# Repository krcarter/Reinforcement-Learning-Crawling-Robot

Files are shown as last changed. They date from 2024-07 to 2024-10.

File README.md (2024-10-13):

# Reinforcement Learning Crawling-Robot

Built a simple quadruped robot that used reinforcement learning for walking. I trained the robot in [Pybullet](https://docs.google.com/document/d/10sXEhzFRSnvFcl3XxNGhnD4N2SedqwdAvK3dsihxVUA/edit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).

Youtube Video: [https://youtu.be/Dv9h6W830aU?si=A5QDVAJMPijuq6lc](https://youtu.be/Dv9h6W830aU?si=A5QDVAJMPijuq6lc)

Table_Crawl  

Pronk Gait 

# Hardware

 URDF files are in the models folder. CAD files (step & STL) are in the hardware folder

# Python Dependencies

* pybullet==3.2.6 (For windows need to also install Microsoft C++ Build Tools)
* matplotlib==3.6.3
* numpy==1.26.4
* gym==0.23.1
* tensorflow == 2.17.0
* stable-baselines3 == 2.3.2
* shimmy == 0.2.1

# Setting up the Training Enviornment

Pronk Sim 

Pybullet's documentation was a little hard for me to first understand on how to setup the learning enviornment. Two main things is 

* initializing the enviornment in the `_init_.py` in the pybullet_envs folder

```
C:\Users\My PC\AppData\Local\Programs\Python\Python311\Lib\site-packages\pybullet_envs
```

Code to add to the `_init_.py`

```
register(
    id='CrawlingRobot-v0',
    entry_point='pybullet_envs:RobotEnv',
    max_episode_steps=1000,
    reward_threshold=1000.0
)
```

* Creating the `robot_env.py`. This is the big code on how to initilize robot into world how to reset, how to step simulation, how to get robot observation, and how to computer reward. This is is the main script that has to be modified

This script also has to be placed inside the pybullet_envs folder

# References (Cool papers)

* Kamidi, Vinay R., Wael Saab, and Pinhas Ben-Tzvi. "Design and analysis of a novel planar robotic leg for high-speed locomotion." 2017 IEEE/RSJ International Conference on Intelligent Robots and Systems (IROS). IEEE, 2017.

* Singla, Abhik, et al. "Realizing learned quadruped locomotion behaviors through kinematic motion primitives." 2019 International Conference on Robotics and Automation (ICRA). IEEE, 2019.

* Tan, Jie, et al. "Sim-to-real: Learning agile locomotion for quadruped robots." arXiv preprint arXiv:1804.10332 (2018).

* Rudin, Nikita, et al. "Learning to walk in minutes using massively parallel deep reinforcement learning." Conference on Robot Learning. PMLR, 2022.

* Schulman, John, et al. "Proximal policy optimization algorithms." arXiv preprint arXiv:1707.06347 (2017).

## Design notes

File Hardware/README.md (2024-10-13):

# Hardware

 To create your own custom URDF for bullet using fusion 360 for CAD checkout this github repo

 * https://github.com/yanshil/Fusion2PyBullet (Need to change the color, remove transmissions)

## Bill of Materials
 
 Amazon affiliate links
 
 [Crawling Robot Bill of Materials](https://docs.google.com/spreadsheets/d/1Qh913g_B4fr31vWqntHaWgeFabi9nsJZdBvG8iXUXsA/edit?usp=sharing)

 1. [4x MG-995 Servos Motors](https://amzn.to/4dJvymz)
 2. [Arduino Uno](https://amzn.to/487Hr4Q)
 3. [PCA9685 Servo Board](https://amzn.to/3Nohsw9)
 4. [2s Lipo Battery 50C 2200mAh](https://amzn.to/3YlSpQM)

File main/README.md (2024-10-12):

# Introduction

This is where the code lies for both the manual and reinforcement learning scripts. First, this code is very rough and was first pass, riddled with a pleothra of bad coind practices. However, this is not production code and is meant to showcase ideas.

## Manual Walking

The two scripts for the manual walking is done in files `ellipsoid_traj_small.py` and `ellipsoid_traj_long.py`

In these scripts is where the math to generate the ellipsoid and then using the forward and inverse kinematics of the legs turn the ellisoid x and y trajectory to joint coordinates for the legs.

The output of the script is done in function 

```
def sim_to_real_text_file(trajectory, num_steps):

```

This outputs a csv and a text file in the format needed to upload to arduino for the joint trajectories that will need to be followed in the Arduino code.

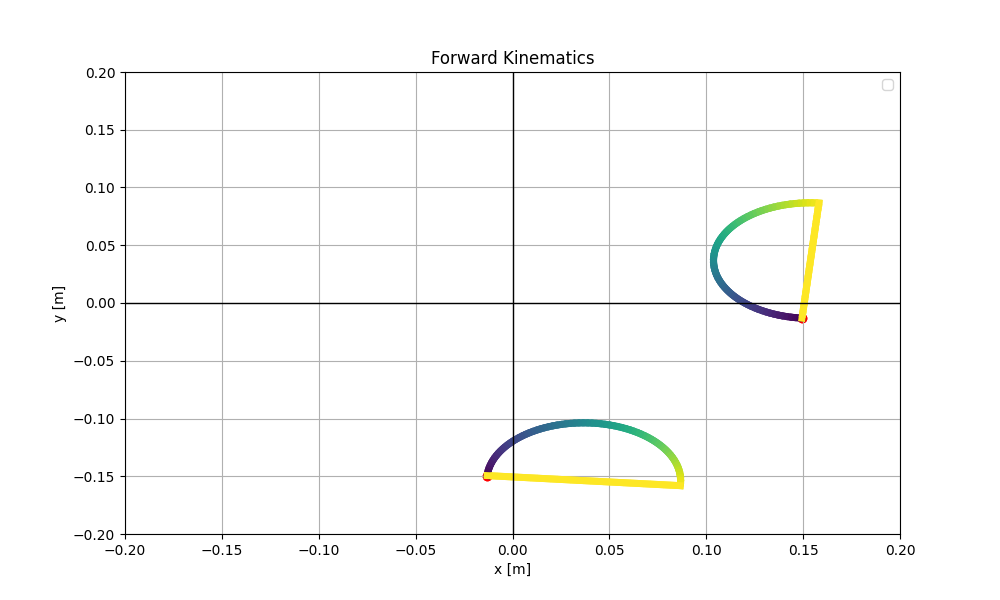
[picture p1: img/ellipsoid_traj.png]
Ellipsoid
 

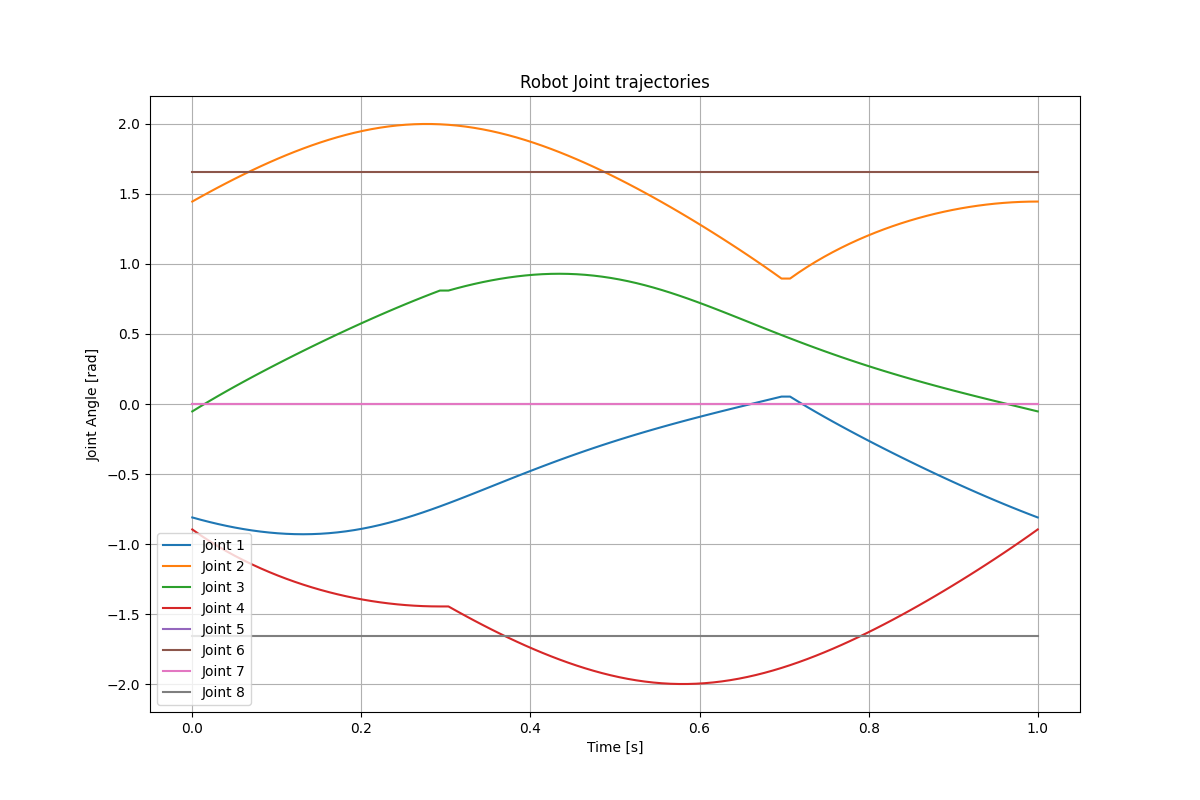
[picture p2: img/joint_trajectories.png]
Joint Trajectories
 

## Running the training

The reinforcement learning pipeline to generate trajectories to put on the robot was running `robot_train.py`, `robot_evaluate.py`, and then `robot_csv_simulation.py`. Also, the `robot_env.py`

### robot_env.py

The create of the enviornment is one of the biggest steps of the pipeline. Some things are probably easiest to adjust are the, action space limits as this controls the minimum and max value of the leg positions

```
action_low  = np.array([ -75,  30,  0, -120, 0,  70, 0, -110]) * np.pi/180
action_high = np.array([   0, 120, 75,  -30, 0,  110, 0,-70]) * np.pi/180
```

Also adjusting the rewards

```
reward = (self._distance_weight * forward_reward 
                  - self._energy_weight * energy_reward 
                  + self._drift_weight * drift_reward 
                  + self._shake_weight * shake_reward
                  + fall_penalty #Penalty for falling
                  )
```

### robot_train.py

To train the robot I used Proximal Policy Optimization (PPO) incorporated through [stable_baseline3](https://stable-baselines3.readthedocs.io/en/master/modules/ppo.html). This script pretty simple it starts the enviornment and run the training for the total amount of time_steps you set. Values to change would be:

```
learning_rate
n_steps
batch_size
total_timesteps

name of the output model
```

The output of this script will be `ppo_robot.py` that holds information about the train model that can be played back in new environemnt instance

### robot_evaluate.py

In robot_evaluate I run the model that I got in robot_train.py, for a few num_steps. The goal here is to get the robot walking for it has a decent walking gait that we can extrapolate later in `robot_csv_simulation.py`. The output of `robot_evaluate.py` is a csv of the joint trajectories of the robot during the model playback.

### read_csv_simulation.py

The `robot_csv_simulation.py` is the last step in my RL pipeline, and it is my hacky way to get the robot trajectories after doing the reinforcement learning. This scripts reads the robot_evaluate.csv produced from `robot_evaluate.py`, and you modify the 

```
start_timestep = 
end_timestep = 
```

Then the script output the trajectories at this time as a text file that can be placed in Arduino .ino file.

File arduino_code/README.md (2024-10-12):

# Arduino Code

After learning was done generated trajectories to put on the real robot that the Arduino script pulled from. Try out the different gait behaviors. To create longer trajectories of more than 100 waypoints the Arduino Uno is going have to be upgraded to a different board.

## RL Crawl Gait vs Manual Crawl Gait

Reinforcement Learning

```
sim_to_real_826_RL.ino
```

Manual Gait 

```
sim_to_real_826_manual.ino
```

RL_Manual Gait

## RL Pronk Gait (Doesn't Work)

```
sim_to_real_pronk_both_legs.ino
```

Pronk Gait

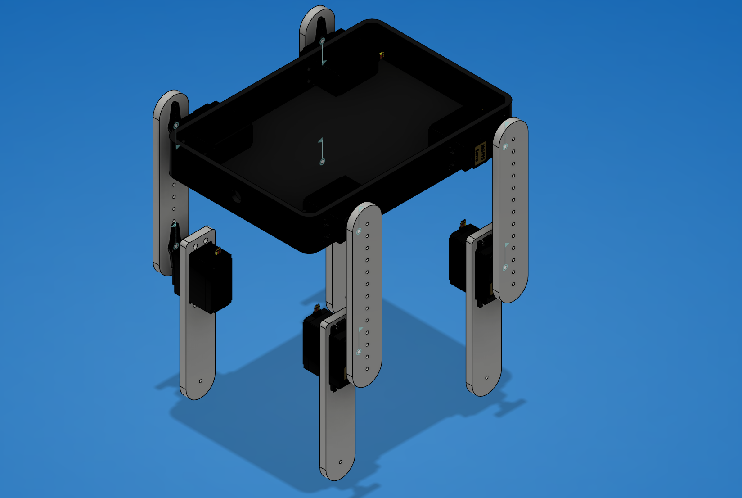
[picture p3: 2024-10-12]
Hardware/long_legs/long_leg.png

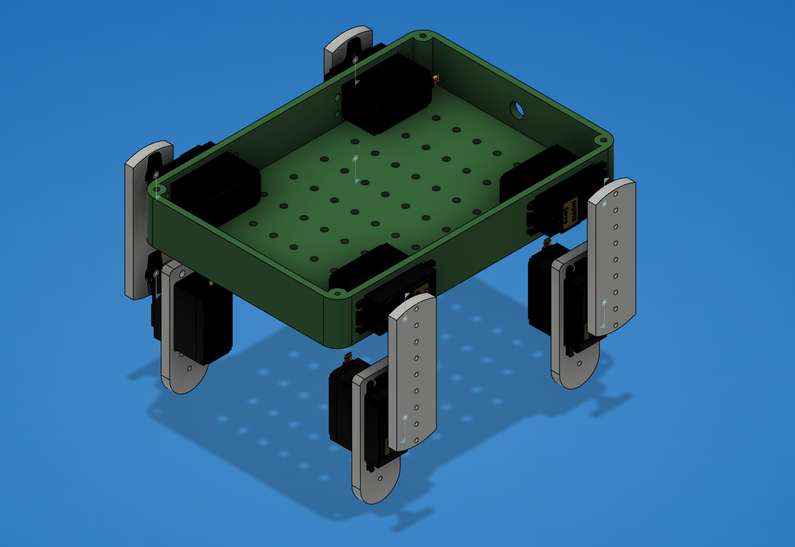
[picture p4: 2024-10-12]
Hardware/short_legs/crawly_short.png

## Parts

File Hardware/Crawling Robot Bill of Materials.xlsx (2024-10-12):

Item | Quantiy | Unit Cost | Total | Link | Notes
[4-Pack] MG996R 55g Metal Gear Torque Digital Servo Motor for Futaba JR RC Helicopter Car Boat Robot | 2 | 16.99 | 33.98 | https://amzn.to/4dJvymz
Arduino Uno REV3 [A000066] | 1 | 27.6 | 27.6 | https://amzn.to/487Hr4Q | Official Arduino Uno a replica can also work
HiLetgo PCA9685 16 Channel 12-Bit PWM Servo Motor Driver IIC Module for Arduino Robot | 1 | 8.99 | 8.99 | https://amzn.to/3Nohsw9 | Documentation here: https://learn.adafruit.com/16-channel-pwm-servo-driver?view=all
OVONIC 2s Lipo Battery 50C 2200mAh 7.4V Lipo Battery with XT60+TRX Connector for RC Car Truck Boat Airplane Helicopter Quadcopter FPV Racing Drone | 1 | 13.4 | 13.4 | https://amzn.to/3YlSpQM | Need to order the proper balancing charger

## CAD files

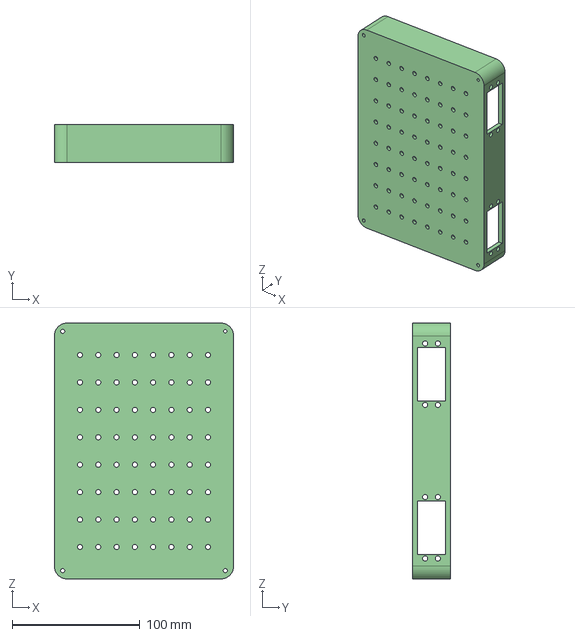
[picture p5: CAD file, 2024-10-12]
Hardware/long_legs/base_link_s.step
140.0 x 30.0 x 200.0 mm

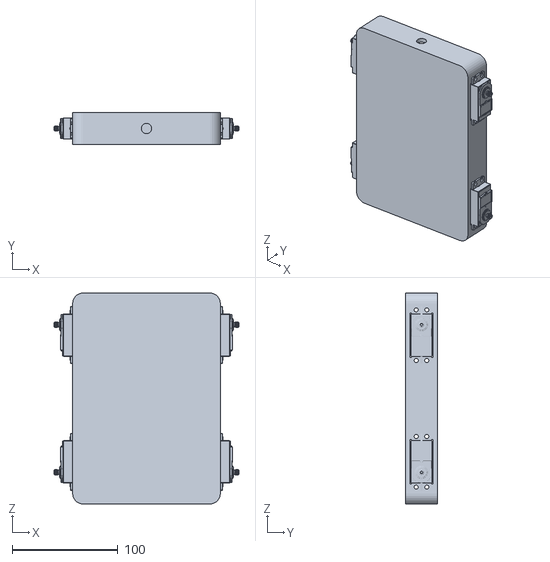
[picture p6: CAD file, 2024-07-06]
main/urdf/meshes/base_link.stl
175.0 x 30.0 x 200.0

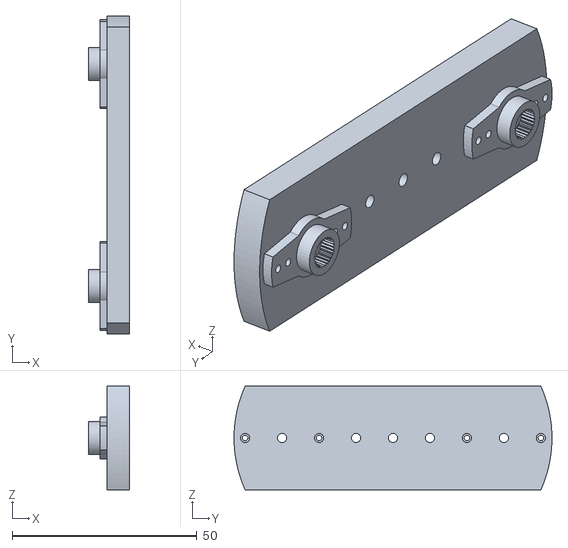
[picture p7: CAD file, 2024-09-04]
main/urdf/small_robot/meshes/L1_BR1.stl
11.0 x 86.0 x 28.0

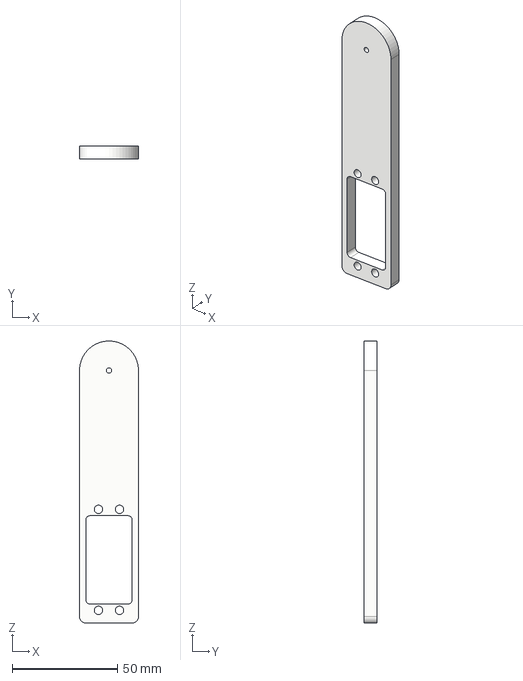
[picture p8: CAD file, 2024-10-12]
Hardware/long_legs/link2.step
28.0 x 6.00 x 134.0 mm

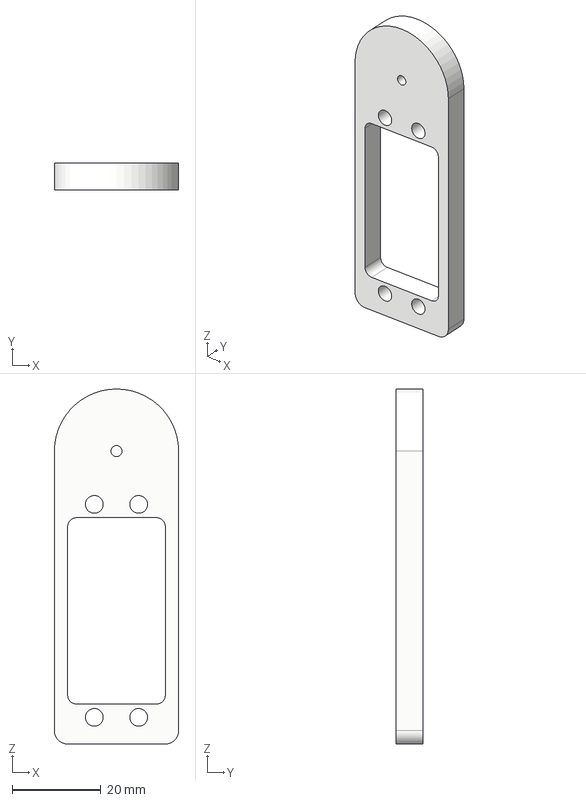
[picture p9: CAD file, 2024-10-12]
Hardware/short_legs/link2_s.step
28.0 x 6.00 x 80.0 mm

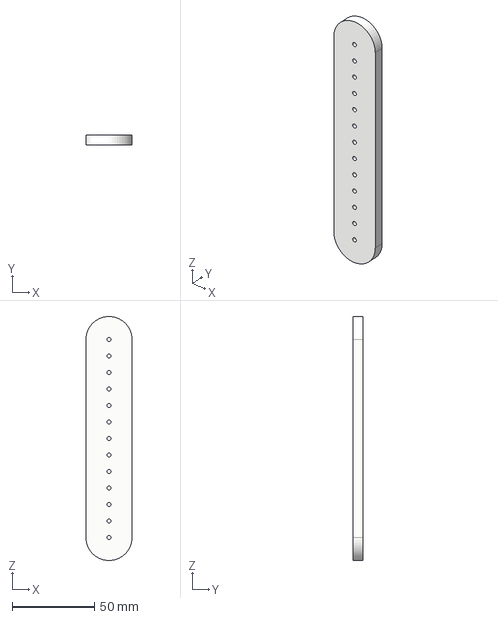
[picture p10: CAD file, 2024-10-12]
Hardware/long_legs/link1.step
28.0 x 6.00 x 148.0 mm

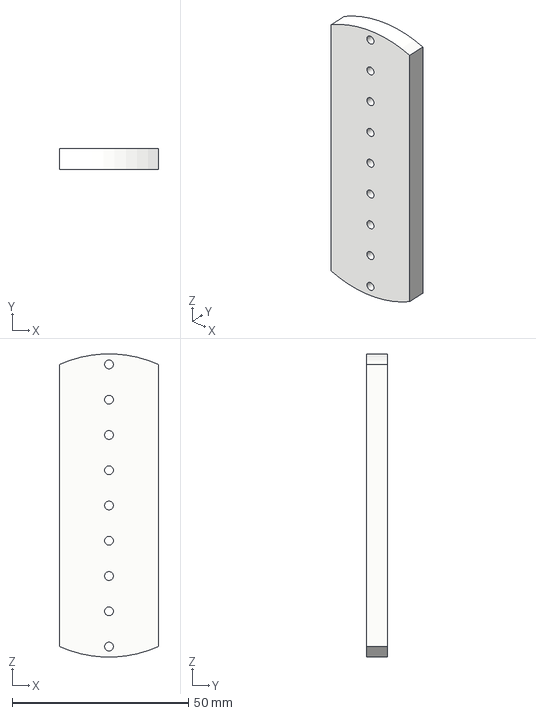
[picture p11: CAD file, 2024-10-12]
Hardware/short_legs/link1_s.step
28.0 x 6.00 x 85.9 mm

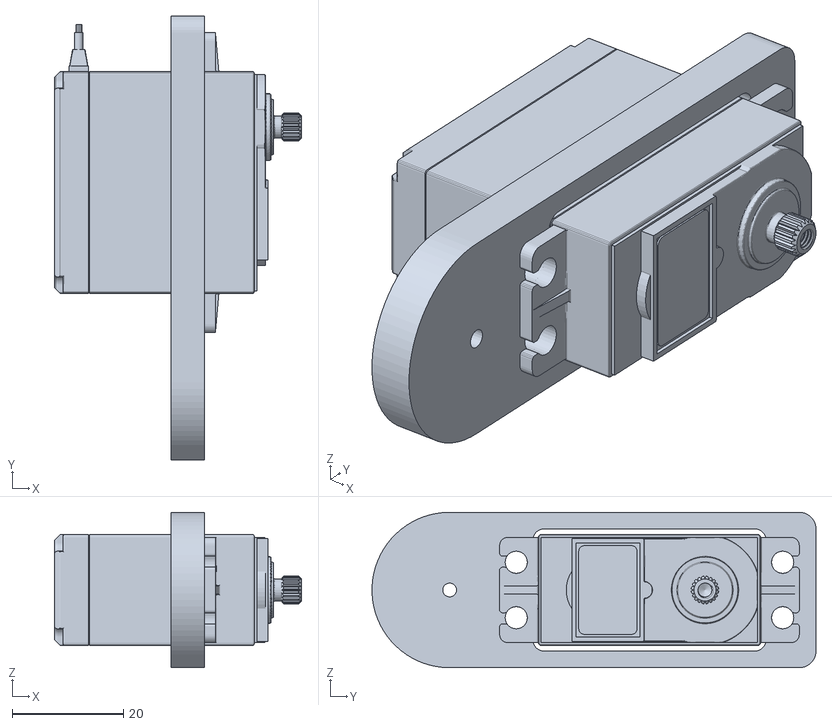
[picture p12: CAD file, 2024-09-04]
main/urdf/small_robot/meshes/L2_BR1.stl
44.5 x 80.0 x 28.0

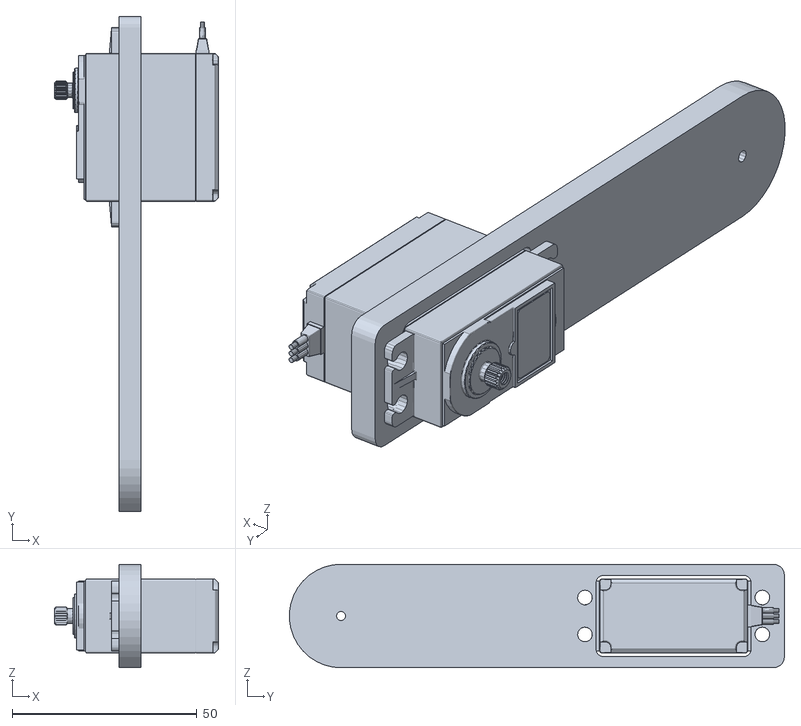
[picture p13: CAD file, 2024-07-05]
main/urdf/meshes/link2_v91.stl
44.5 x 134.0 x 28.0

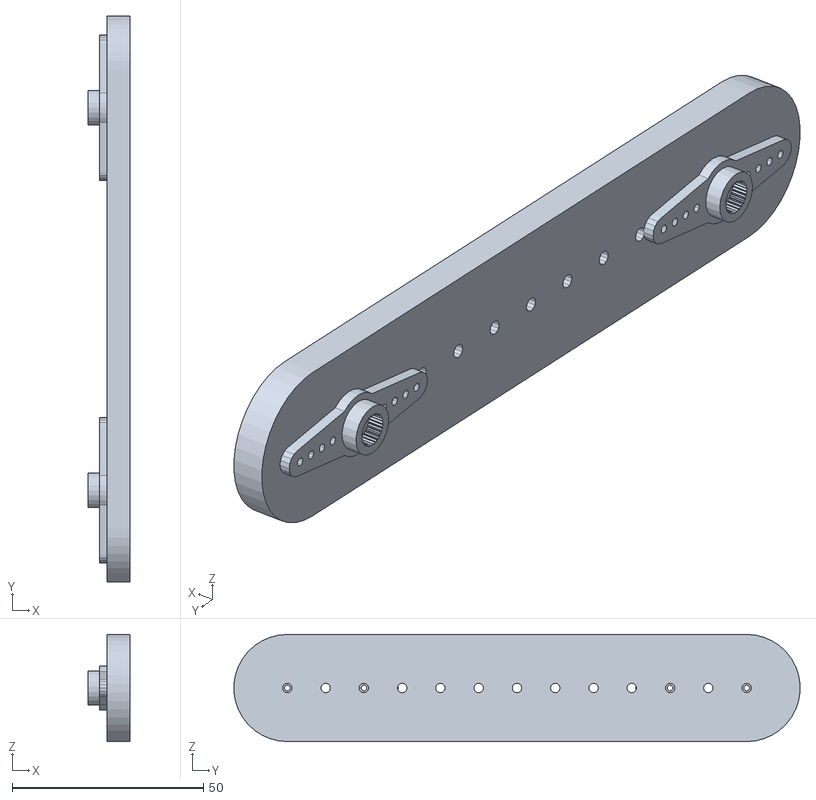
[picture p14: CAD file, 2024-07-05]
main/urdf/meshes/link1_v131.stl
11.0 x 147.9 x 28.0

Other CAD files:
main/urdf/small_robot/meshes/base_link.stl
main/urdf/small_robot/meshes/L1_BL1.stl
main/urdf/small_robot/meshes/L1_FR1.stl
main/urdf/small_robot/meshes/L2_BL1.stl
main/urdf/small_robot/meshes/L1_FL1.stl
main/urdf/small_robot/meshes/L2_FR1.stl
main/urdf/small_robot/meshes/L2_FL1.stl
Hardware/long_legs/base_link_s.stl
Hardware/long_legs/link1.stl
Hardware/long_legs/link2.stl
Hardware/short_legs/base_link_s.stl
Hardware/short_legs/link1_s.stl
Hardware/short_legs/link2_s.stl
main/urdf/meshes/link1_v13_11.stl
main/urdf/meshes/link1_v13_21.stl
main/urdf/meshes/link1_v13_31.stl
main/urdf/meshes/link2_v9_11.stl
main/urdf/meshes/link2_v9_21.stl
main/urdf/meshes/link2_v9_31.stl

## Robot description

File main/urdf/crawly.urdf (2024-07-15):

<?xml version="1.0" ?>
<robot name="crawly2">

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

<link name="base_link">
  <inertial>
    <origin xyz="4.450311950833269e-16 0.01206888961783032 -8.8091820405535e-05" rpy="0 0 0"/>
    <mass value="0.37046418538360243"/>
    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
  </inertial>
  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
</link>

<link name="L1_BL1">
  <inertial>
    <origin xyz="0.004791729434917569 -0.05000000000000002 6.342149028171207e-15" rpy="0 0 0"/>
    <mass value="0.026073176545293626"/>
    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
  </inertial>
  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
</link>

<link name="L1_BR1">
  <inertial>
    <origin xyz="-0.004791729434917569 -0.05000000000000002 -6.300515664747763e-15" rpy="0 0 0"/>
    <mass value="0.026073176545293626"/>
    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
  </inertial>
  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
</link>

<link name="L1_FR1">
  <inertial>
    <origin xyz="-0.004791729434917569 -0.05000000000000002 -6.369904603786836e-15" rpy="0 0 0"/>
    <mass value="0.026073176545293626"/>
    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
  </inertial>
  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
</link>

<link name="L1_FL1">
  <inertial>
    <origin xyz="0.004791729434917569 -0.05000000000000002 6.2727600891321345e-15" rpy="0 0 0"/>
    <mass value="0.026073176545293626"/>
    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
  </inertial>
  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
</link>

<link name="L2_FR1">
  <inertial>
    <origin xyz="0.024243020603580356 -0.021200077196389333 4.128034769707023e-07" rpy="0 0 0"/>
    <mass value="0.072990131570421"/>
    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
  </inertial>
  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
</link>

<link name="L2_FL1">
  <inertial>
    <origin xyz="-0.024243020603580356 -0.021200077196389333 -4.1280347701233566e-07" rpy="0 0 0"/>
    <mass value="0.072990131570421"/>
    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
  </inertial>
  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
</link>

<link name="L2_BR1">
  <inertial>
    <origin xyz="0.024243020603580356 -0.021200077196389333 4.128034769984579e-07" rpy="0 0 0"/>
    <mass value="0.072990131570421"/>
    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
  </inertial>
  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
</link>

<link name="L2_BL1">
  <inertial>
    <origin xyz="-0.024243020603580356 -0.021200077196389305 -4.128034769707023e-07" rpy="0 0 0"/>
    <mass value="0.072990131570421"/>
    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
  </inertial>
  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
</link>

<joint name="th_1" type="revolute">
  <origin xyz="0.0875 0.015 0.07" rpy="0 0 0"/>
  <parent link="base_link"/>
  <child link="L1_FL1"/>
  <axis xyz="-1.0 0.0 0.0"/>
  <limit effort="1.18" lower="-3.14159" upper="3.14159" velocity="8.05"/>
</joint>

<joint name="th_2" type="revolute">
  <origin xyz="-0.0875 0.015 0.07" rpy="0 0 0"/>
  <parent link="base_link"/>
  <child link="L1_FR1"/>
  <axis xyz="1.0 0.0 0.0"/>
  <limit effort="1.18" lower="-3.14159" upper="3.14159" velocity="8.05"/>
</joint>

<joint name="th_3" type="revolute">
  <origin xyz="-0.0875 0.015 -0.07" rpy="0 0 0"/>
  <parent link="base_link"/>
  <child link="L1_BR1"/>
  <axis xyz="1.0 0.0 0.0"/>
  <limit effort="1.18" lower="-3.14159" upper="3.14159" velocity="8.05"/>
</joint>

<joint name="th_4" type="revolute">
  <origin xyz="0.0875 0.015 -0.07" rpy="0 0 0"/>
  <parent link="base_link"/>
  <child link="L1_BL1"/>
  <axis xyz="-1.0 0.0 0.0"/>
  <limit effort="1.18" lower="-3.14159" upper="3.14159" velocity="8.05"/>
</joint>


<joint name="th_5" type="revolute">
  <origin xyz="0.0 -0.1 0.0" rpy="0 0 0"/>
  <parent link="L1_FL1"/>
  <child link="L2_FL1"/>
  <axis xyz="-1.0 -0.0 0.0"/>
  <limit effort="1.18" lower="-3.14159" upper="3.14159" velocity="8.05"/>
</joint>

<joint name="th_6" type="revolute">
  <origin xyz="0.0 -0.1 0.0" rpy="0 0 0"/>
  <parent link="L1_FR1"/>
  <child link="L2_FR1"/>
  <axis xyz="1.0 -0.0 -0.0"/>
  <limit effort="1.18" lower="-3.14159" upper="3.14159" velocity="8.05"/>
</joint>

<joint name="th_7" type="revolute">
  <origin xyz="0.0 -0.1 0.0" rpy="0 0 0"/>
  <parent link="L1_BR1"/>
  <child link="L2_BR1"/>
  <axis xyz="1.0 -0.0 -0.0"/>
  <limit effort="1.18" lower="-3.14159" upper="3.14159" velocity="8.05"/>
</joint>

<joint name="th_8" type="revolute">
  <origin xyz="0.0 -0.1 0.0" rpy="0 0 0"/>
  <parent link="L1_BL1"/>
  <child link="L2_BL1"/>
  <axis xyz="-1.0 -0.0 0.0"/>
  <limit effort="1.18" lower="-3.14159" upper="3.14159" velocity="8.05"/>
</joint>


</robot>

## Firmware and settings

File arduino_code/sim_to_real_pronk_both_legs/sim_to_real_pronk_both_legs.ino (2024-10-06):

#include "positions.h"  // Include the positions header file
#include <Wire.h>
#include <Adafruit_PWMServoDriver.h>
#include <math.h>


// called this way, it uses the default address 0x40
Adafruit_PWMServoDriver pwm = Adafruit_PWMServoDriver();

// Setting up positioning for servos
#define SERVOMIN  100 // This is the 'minimum' pulse length count (out of 4096)
#define SERVOMAX  505 // This is the 'maximum' pulse length count (out of 4096)
#define SERVO_FREQ 50 // MF95 update rate of 50


unsigned long previousMillis = 0;
const long updateInterval = 40;  // updateInterval in milliseconds

int currentPosition = 0;

void setup() {
  Serial.begin(9600);
  Serial.println("Simulation to Real");

  pwm.begin();
  pwm.setPWMFreq(SERVO_FREQ);  // Analog servos run at ~50 Hz updates

  delay(10);

  // HACKY but wanted get this up and running quick
  // Set Back legs intials conditions

  int J4 = map(90, 0, 180, SERVOMIN, SERVOMAX);
  int J5 = map(90, 0, 180, SERVOMIN, SERVOMAX);
  int J6 = map(90, 0, 180, SERVOMIN, SERVOMAX);
  int J7 = map(90, 0, 180, SERVOMIN, SERVOMAX);

  pwm.setPWM(4, 0, J4);
  pwm.setPWM(5, 0, J5);
  pwm.setPWM(6, 0, J6);
  pwm.setPWM(7, 0, J7);
}

void loop() {
  unsigned long currentMillis = millis();

  if (currentMillis - previousMillis >= updateInterval) {
    previousMillis = currentMillis;

    // Set the servo to the current position
    Serial.print(currentPosition);
    Serial.print(":  ");
    Serial.print(row_1[currentPosition]);
    Serial.print(", ");
    Serial.print(row_2[currentPosition]);
    Serial.print(", ");
    Serial.print(row_3[currentPosition]);
    Serial.print(", ");
    Serial.println(row_4[currentPosition]);


    int J0 = map(row_1[currentPosition], 0, 180, SERVOMIN, SERVOMAX);
    int J1 = map(row_2[currentPosition], 0, 180, SERVOMIN, SERVOMAX);
    int J2 = map(row_3[currentPosition], 0, 180, SERVOMIN, SERVOMAX);
    int J3 = map(row_4[currentPosition], 0, 180, SERVOMIN, SERVOMAX);

    int J4 = map(row_5[currentPosition], 0, 180, SERVOMIN, SERVOMAX);
    int J5 = map(row_6[currentPosition], 0, 180, SERVOMIN, SERVOMAX);
    int J6 = map(row_7[currentPosition], 0, 180, SERVOMIN, SERVOMAX);
    int J7 = map(row_8[currentPosition], 0, 180, SERVOMIN, SERVOMAX);

    pwm.setPWM(0, 0, J0);
    pwm.setPWM(1, 0, J1);
    pwm.setPWM(2, 0, J2);
    pwm.setPWM(3, 0, J3);

    pwm.setPWM(4, 0, J4);
    pwm.setPWM(5, 0, J5);
    pwm.setPWM(6, 0, J6);
    pwm.setPWM(7, 0, J7);

    // Move to the next position
    currentPosition++;

    // Loop back to the beginning if at the end
    if (currentPosition >= numPositions) {
      currentPosition = 0;
    }
  }
}

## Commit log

2024-07-05 1st commit with urdf and simple pybullet test
    [base_link.stl, crawly.urdf, link1_v131.stl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]
2024-07-05 Chnage color and initial position when URDF loads in
    [crawly.urdf]
2024-07-06 Rename created URDF with better joint and link naming scheme
    [L1_BL1.stl, L1_BR1.stl, L1_FL1.stl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]
2024-07-06 Modified URDF for joint are numbered properly adding some debugging code for load urdf
    [crawly.urdf]
2024-07-06 Testing Revolute Joint
    [crawly.urdf]
2024-07-06 Enabled Joint Force Torque Sensors
2024-07-06 Added more logging joint, links, base, bodies
2024-07-07 Change camera perspective
2024-07-09 Revolute URDF
    [crawly.urdf]
2024-07-15 Added STL and othere adjustments
    [base_link v18.stl, cover v8.stl, crawly.urdf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]
2024-07-19 Move URDF location
    [L1_BL1.stl, L1_BR1.stl, L1_FL1.stl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]
2024-07-20 Fix bug where the robot did not start flat on ground
2024-07-22 Adding action space for back legs
2024-07-27 Arduino Position and sine sweep code
2024-07-28 Added Manual crawling arduino logic
2024-07-29 Going upload in this state however waiting on voltage regulator to see if this is working code
2024-08-05 Fixed Forward Kinematics, Add all joints to single postion test, incremetn from a starting point
2024-08-05 Plotting both rotated and non rotated leg position for better visualization
2024-08-07 Process of fixing stance/swing gaits need right leg to step out first
2024-08-08 working two legs moving at the same time
2024-08-09 working on sim to real
    [trajectory.csv]
2024-08-09 mapped simualation to real except Joint 1
    [trajectory.csv]
2024-08-09 Succesfully Flip signs
    [trajectory.csv]
2024-08-10 Remove deprecated debugging print statements and left comments to keep track of array sizes
2024-08-15 Change leg limits
2024-08-15 Big changes to robot_evaluate.py have the simulation output those joint positions and graph them
2024-08-16 Made new arduino script for the bounding gait
    [sim_trajectory_bound.csv]
2024-08-16 Moving arduino trajectories to different folder
2024-08-17 Added new arduino script for forward reward robot
    [sim_trajectory.csv, sim_trajectory_811.csv, sim_trajectory_816.csv]
2024-08-17 Got the right trajectory transformation for the sim to real
    [sim_trajectory.csv, sim_trajectory_816_2.csv]
2024-08-18 Ahh lets of changes
    [ellipsoidCheck.csv, sim_trajectory.csv, sim_trajectory_817_crawl.csv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]
2024-08-26 Commit before add ability to reorder walk trajectory
    [ellipsoidCheck.csv, sim_trajectory.csv, trajectory.csv]
2024-08-26 [BIG Change] - Properly made joint trajectory switch between stance and swing
    [ellipsoidCheck.csv, trajectory.csv]
2024-08-26 added 8_26 stance swing switch
    [trajectory.csv]
2024-08-27 NEW TRAJECTORY FINALLY WORKED
    [sim_trajectory.csv, sim_trajectory_26.csv]
2024-09-04 Big change to have a smaller crawling robot
    [L1_BL1.stl, L1_BR1.stl, L1_FL1.stl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]
2024-09-04 Change the folder where elippse_traj gets the urdf
    [ellipsoidCheck.csv, trajectory.csv]
2024-09-05 okay kind of a lot going on here but main thing seperated into eliposd_traj and one for when robot was long
    [ellipsoidCheck.csv, sim_trajectory.csv, trajectory.csv]
2024-09-15 switch_urdf for quick test
    [L1_BL1.stl, L1_BR1.stl, L1_FL1.stl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]
2024-10-02 change so bottom legs are flat
    [ellipsoidCheck.csv, trajectory.csv]
2024-10-06 Made pronk gait
    [best_crawl.csv, ellipsoidCheck.csv, full_bound.csv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]
2024-10-12 Add step and stl files
    [Crawling Robot Bill of Materials.xlsx, base_link v18.stl, base_link_s.step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]
2024-10-12 Change License file and remove arduino files that were not pronk,rl,manul gait
2024-10-12 Cleaning out the main folder
    [ellipsoidCheck.csv, sim_trajectory.csv, sim_trajectory_26.csv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]
2024-10-12 Cleaned up main code folder
    [manual_walk_long.csv, manual_walk_short.csv]
2024-10-12 remove csv and txt files
    [best_crawl.csv, full_bound.csv, manual_walk_long.csv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]
